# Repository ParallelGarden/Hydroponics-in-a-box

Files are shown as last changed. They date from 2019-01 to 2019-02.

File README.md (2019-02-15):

# Hydroponics-in-a-box

## EXPERIMENTAL DESIGN FEATURE TO GROW PLANTS IN A CAFE

### PURPOSE

This hydroponics box was custom developed to fit under the bar in Bitcoin Coffee at Paralelní Polis in Prague. This hydroponic box uses the drip irrigation principle. It serves as special design feature where vegetables can be grown for the purpose of the cafe, to study production process, to communicate the technology with the public, and to conduct workshops on growing in hydroponics. Thebox was designed in a way to be as compact as possible in order to avoid external solution reservoir, exposed wiring, etc. This project consists of two projects that form a compatible outcome product: hydroponics system itself, and IoT device that is being developed in order to collect data about the growing process, optimize costs, and eventually to take control over the system.

This initiative is a project related to the Enviro Meetup programme we are running in Paralelní Polis in Prague. Our activities are being live streamed through the facebook of Paralelní Polis [https://www.facebook.com/vejdiven/](https://www.facebook.com/vejdiven/) . Then they are being uploaded to youtube under following link: [https://www.youtube.com/watch?v=hhW6fsABNEE&list=PLGJQS0h-wqLQ6r8_6Ans_e26NkKsHYUh-](https://www.youtube.com/watch?v=hhW6fsABNEE&list=PLGJQS0h-wqLQ6r8_6Ans_e26NkKsHYUh-) We would love to enable the content for English speakers as well, and we would appreciate any initiative to help us with translation from Czech to English and subtitles addition into our videos.

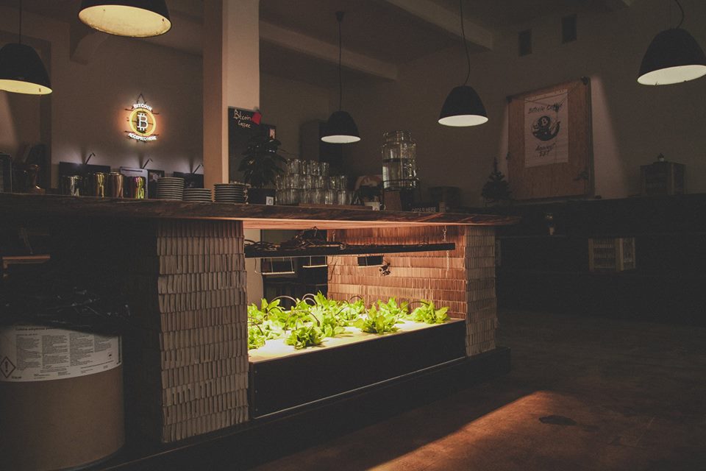
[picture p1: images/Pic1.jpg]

[Photo by: pedro__35mm](https://www.instagram.com/pedro__35mm/)

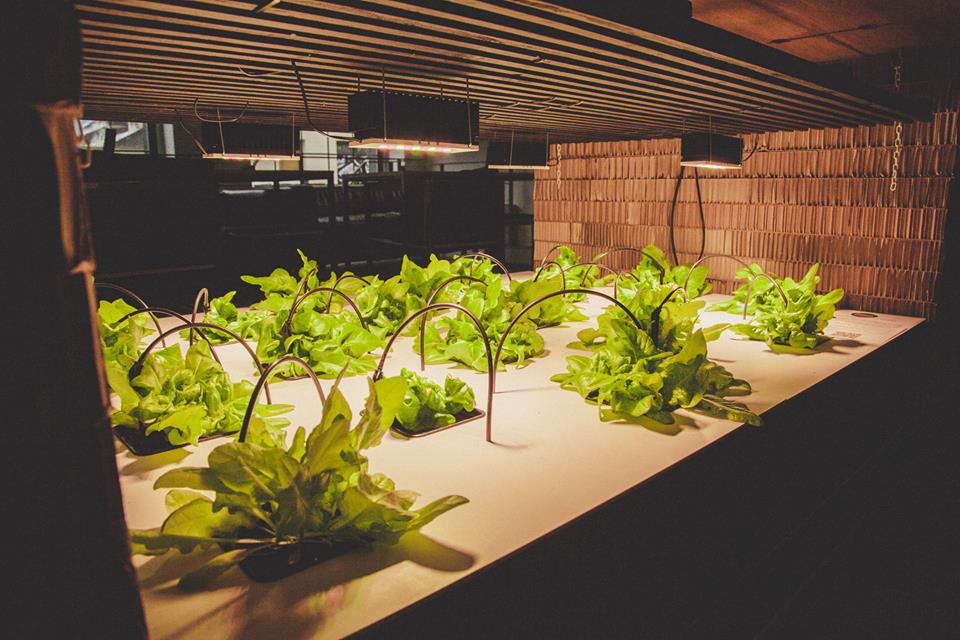
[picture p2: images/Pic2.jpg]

[Photo by: pedro__35mm](https://www.instagram.com/pedro__35mm/)

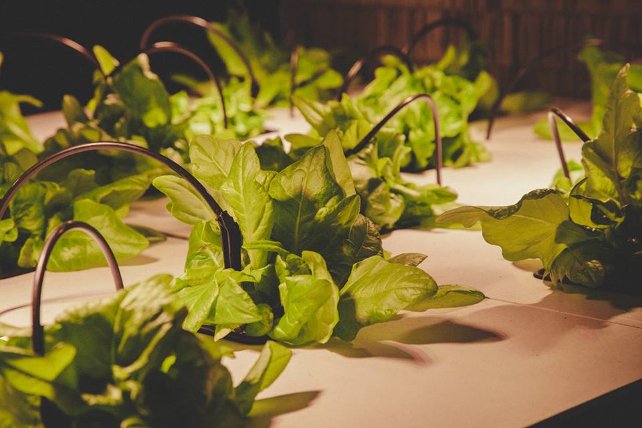
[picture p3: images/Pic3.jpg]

[Photo by: pedro__35mm](https://www.instagram.com/pedro__35mm/)

### OPEN SOURCE REPOSITORIES AND DEVELOPMENT

#### Hydroponics system

Full documentation about this project may be found in the Github repository under following link:  [https://github.com/ParallelGarden/Hydroponics-in-a-box](https://github.com/ParallelGarden/Hydroponics-in-a-box) 

NOTICE! We understand somebody might not be familiar with Github. If you would like to contribute to the development, but don't know how to do so, please feel free to send your suggestions via e-mail: jakub.hamata@gmail.com

##### Development road map:

* Lights - We are overal interested in finding the perfect fit lights for our system to ipmrove the effectivity of the growing system. Crucial deliverables are: cost of the light, electricity consumption, and suitability. Current lights are full spectrum LED which is great for growing both leafy and fruit vegetables. However we need quite many of them due to the space limitation, and they are quite strong (causing little burning of edges of leaves). The angle of the light beam is quite narrow for the space.

* Growing substrates - At the beginning we started with realiable substrates such as coconut fibre substrate, or rockwool cubes. We are interested in finding a substrate that can be produced locally, and is biodegradable. Coconut substrates are the last option as this material has to be imported from other parts of the world.

* Fertilizers - We are looking for an organic fertilizer (or mix of organic fertilizers) to establish the production in bio quality. We are very limited by hygienic standards of the place as it is completely exposed. We must avoid any unpleasand smell or breeding of pests.

* Technologies and processes - Please have a look at our datasheet regarding the cost of the production under following link [https://github.com/ParallelGarden/Hydroponics-in-a-box/blob/master/datasheets/EconomicsOfTheProduction.pdf](https://github.com/ParallelGarden/Hydroponics-in-a-box/blob/master/datasheets/EconomicsOfTheProduction.pdf) We will appreciate any contributions regarding the technology that can reduce production costs or tips to reduce the time consumption of the labour. In case of labour we would like to reduce time consumption on following operations: preparation of seedlings, and regular cleanup of the system.

##### IoT device

Full documentation about this project may be found in the Github repository under following link:[https://github.com/octopusengine/octopusLAB_parallel_garden](https://github.com/octopusengine/octopusLAB_parallel_garden)

Collected database is accessible under following link:

[http://www.octopusengine.org/api/hydrop/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](http://www.octopusengine.org/api/hydrop/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)

Created by Jakub Hamata

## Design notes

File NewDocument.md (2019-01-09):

# New Document

hello world
* gggg
* ggg
* ggg

#
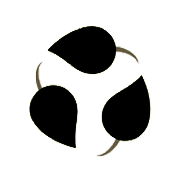
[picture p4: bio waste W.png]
obrazek vole


1. list 1
2. dfdfd
2. fdfdfd
3. gggg
4. gggg

### 444
## ff
###### ssss

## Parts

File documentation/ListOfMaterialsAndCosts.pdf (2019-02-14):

# HYDROPONICS IN THE BOX

## List of materials and costs

Conversion rate: 1USD = 21,5CZK (Jan2019)
Article character: VAR = variable = we encourage to substitute the article by any cheaper, but suitable material

## RESERVOIR

N.O. | Article character | Name | Material specification | Unit | Unit cost (CZK) | Quantity | Total cost (CZK) | Total cost (USD)
1 | FIX | Plywood board | 96x20x2cm (black finish) | each | 173 | 2 | 346 | 16
2 | FIX | Plywood board | 150x20x2cm (black finish) | each | 346 | 2 | 692 | 32
3 | FIX | Screws | 4x40 | each | 2 | 12 | 24 | 1
4 | VAR | Plastic board | 150x100x0,5cm | each | 896 | 1 | 896 | 42
5 | FIX | Screws | 3x40 | each | 2 | 46 | 92 | 4
6 | VAR | Plastic board | 146x96x0,5cm | each | 896 | 1 | 896 | 42
7 | VAR | Plastic board | 146x18x0,5cm | each | 224 | 2 | 448 | 21
8 | VAR | Plastic board | 95x18x0,5cm | each | 224 | 2 | 448 | 21
9 | FIX | Glue for plastics | 0,5l | each | 120 | 1 | 120 | 6
10 | FIX | Plumbers putty | 280ml | each | 144 | 0,4 | 57,6 | 3
4020 187

## MIDDLE FLOOR

N.O. | Article character | Name | Material specification | Unit | Unit cost (CZK) | Quantity | Total cost (CZK) | Total cost (USD)
1 | VAR | Plastic board | 95x72,5x0,5 | each | 448 | 2 | 896 | 42
2 | FIX | Plastic anchors for styrofoam heat insulation | Length 6cm | each | 10 | 21 | 210 | 10
3 | FIX | Plumbers putty | | each | 144 | 0,3 | 43,2 | 2
Total | | | | | | | 1149 53

## TOP BOARD

N.O. | Article character | Name | Material specification | Unit | Unit cost (CZK) | Quantity | Total cost (CZK) | Total cost (USD)
1 | FIX | Plastic board | 75x100x0,5 | each | 448 | 2 | 896 | 42
2 | FIX | Plastic board | 72,5x95x0,5 | each | 448 | 2 | 896 | 42
3 | FIX | Plastic anchors for styrofoam heat insulation | Length 12,5cm | each | 10 | 10 | 100 | 5
4 | FIX | Plumbers putty | | each | 144 | 0,15 | 22 | 1
Total | | | | | | | 1914 89

Total

## IRRRIGATION

N.O. | Article character | Name | Material specification | Unit | Unit cost (CZK) | Quantity | Total cost (CZK) | Total cost (USD)
1 | FIX | Plastic pipe holder | Diameter 1,5cm | each | 5,5 | 14 | 77 | 4
2 | FIX | Plastic pipe | Diameter 1,5cm | m | 8,5 | 6 | 51 | 2
3 | FIX | Plastic pipe L connection | Diameter 1,5cm | each | 15 | 8 | 120 | 6
4 | FIX | Plastic pipe T connection | Diameter 1,5cm | each | 39 | 2 | 78 | 4
5 | FIX | Plastic hose | Diameter 1,5cm | m | 35 | 1 | 35 | 2
6 | FIX | Plastic hose L connections | Diameter 1,5cm | each | 39 | 2 | 78 | 4
7 | FIX | Plastic flow regulator | 4L/h | each | 12 | 22 | 264 | 12
8 | FIX | Plastic capillary pipes | | m | 10 | 6,3 | 63 | 3
9 | FIX | Plastic dripping needle | | each | 5 | 21 | 105 | 5
10 | FIX | Super glue | | each | 90 | 1 | 90 | 4
11 | FIX | Submersible water pump | 750l/h | each | 399 | 1 | 399 | 19
12 | FIX | Lever cable connecter | | each | 20 | 2 | 40 | 2
13 | FIX | Analog timer | | each | 100 | 1 | 100 | 5
Total | | | | | | | 1500 70

## LIGHTING SYSTEM

N.O. | Article character | Name | Material specification | Unit | Unit cost (CZK) | Quantity | Total cost (CZK) | Total cost (USD)
1 | FIX | Wooden prism | 150x2x2cm | each | 48 | 17 | 816 | 38
2 | FIX | Wooden prism | 99x5x2cm | each | 62 | 3 | 186 | 9
3 | FIX | Nails | 3cm | each | 1 | 51 | 51 | 2
4 | FIX | Steel hooks with screw | | each | 2 | 4 | 8 | 1
5 | VAR | Full spectrum LED lights | SANlight M30 30W | each | 3599 | 4 | 14396 | 670
6 | FIX | Analog timer | | each | 100 | 1 | 100 | 5
Total | | | | | | | 15557 724
| CZK | USD
TOTAL | 24139 | 1123

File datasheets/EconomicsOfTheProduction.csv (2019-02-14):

ECONOMICS OF THE PRODUCTION
Leaf lettuce result per harvest
Growing period: 10 days seedlings preparation + 21 days growing in the hydroponics system
Conversion rate: 1USD = 21,5CZK (Jan2019)
COSTS
N.O. | Material | Work | Specification | Unit | Unit cost CZK | Quantity | Cost CZK | Cost USD
1 | Electricity |  |  | 1 kWh | 5 | 30,24 | 151 | 7
2 | Water |  |  | 1 m3 | 89,66 | 0,07 | 6 | 0
3 | Fertilizer |  | General Hydroponics FloraNova Grow 473ml /16 OZ | each | 529 | 0,14 | 74 | 3
4 | Substrate |  | Rockwool cube 3,6 x 3,6cm | each | 4 | 21 | 84 | 4
5 | Seeds |  |  | package | 15 | 0,1 | 2 | 0
6 |  | Sowing | NET income 20.000CZK/month | h | 230 | 0,25 | 58 | 3
7 |  | Planting | NET income 20.000CZK/month | h | 230 | 0,75 | 173 | 8
8 |  | System checking | NET income 20.000CZK/month | h | 230 | 1 | 230 | 11
9 |  | System maintenance | NET income 20.000CZK/month | h | 230 | 1 | 230 | 11
TOTAL COST: |  |  |  |  |  |  | 1007CZK | 47USD
WORK: |  |  |  |  |  |  | 690CZK | 32USD
ENERGIES AND MATERIALS: |  |  |  |  |  |  | 317CZK | 15USD
REVENUE
N.O. | Product | Unit | Quantity | Usual retail price CZK | Revenue CZK | Revenue in USD
1 | Lettuce | each | 21 | 30 | 630 | 29
RESULT
1) | In current setup it is not possible to become profitable with usual retail price of lettuce. One lettuce has to be sold for at least 48CZK / 2,23USD.
2) | Main articles are: electricity consumption, and labour. Reduction in these articles could bring positive result.
COMMENTS
1) | It was not inteded to create positive economical outcome with the first hydroponic system.
2) | Hydroponic system brings also other values than just money.
3) | Very likely it is possible to sell the product for higher price than usual retail price of conventional agriculture product.
4) | It would be a great success to manage to reduce production costs to end up on even result (no profit, and no loss).
POTENTIAL OF CURRENT TECHNOLOGY
If we had more space available we could grow twice as many lettuces with only slight increment of the investment cost (larger box), same amount of lights, etc.
Find below a study for double sized box:
COSTS
N.O. | Material | Work | Specification | Unit | Unit cost CZK | Quantity | Cost CZK | Cost USD
1 | Electricity |  |  | 1 kWh | 5 | 30,24 | 151 | 7
2 | Water |  |  | 1 m3 | 89,66 | 0,07 | 6 | 0
3 | Fertilizer |  | General Hydroponics FloraNova Grow 473ml /16 OZ | each | 529 | 0,14 | 74 | 3
4 | Substrate |  | Rockwool cube 3,6 x 3,6cm | each | 4 | 42 | 168 | 8
5 | Seeds |  |  | package | 15 | 0,2 | 3 | 0
6 |  | Sowing | NET income 20.000CZK/month | h | 230 | 0,5 | 115 | 5
7 |  | Planting | NET income 20.000CZK/month | h | 230 | 1,5 | 345 | 16
8 |  | System checking | NET income 20.000CZK/month | h | 230 | 1 | 230 | 11
9 |  | System maintenance | NET income 20.000CZK/month | h | 230 | 1,5 | 345 | 16
TOTAL COST: |  |  |  |  |  |  | 1438CZK | 67USD
WORK: |  |  |  |  |  |  | 1035CZK | 48USD
ENERGIES AND MATERIALS: |  |  |  |  |  |  | 403CZK | 19USD
REVENUE
N.O. | Product | Unit | Quantity | Usual retail price CZK | Revenue CZK | Revenue in USD
1 | Lettuce | each | 42 | 30 | 1260 | 59
RESULT
1) | In current setup it is not possible to become profitable with usual retail price of lettuce. One lettuce has to be sold for at least 35CZK / 1,63USD.
2) | Optimization of cost of labour, substrate, fertilizer, and utilization of daylight appear to be a way to find a profitable model.
3) | Shortening the period of having lettuce in the system also appears to be a way to rech even or positive result.
4) | Another way to go might be to chose a different crop to grow.

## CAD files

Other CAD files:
documentation/dwg drawing/HydroponicsInTheBox1.0.dwg

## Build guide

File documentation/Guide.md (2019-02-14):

# STEP BY STEP GUIDE

## INTRODUCTION

This hydroponic system was developed as a custom design feature for Bitcoin Coffee in Parallel Polis. It is meant to supply the Cafe with specific vegetables that are being used there (mostly leaf vegetables). It also serves for experiments that are combining growing in hydroponic system, IoT technologies, and open source in order to reach as much autonomity of the system as possible that is able to optimize growing process, and energy consumption to the most reasonable effectivity.







## TOOLS

* Drilling machine
* Screw driver
* Glue gun (depending of the type of the glue)
* Paint brush (10cm or wider)
* NT cutter
* Personal protection equipment

## RESERVOIR CONSTRUCTION

### LIST OF MATERIALS:

* Plywood board 96x20x2cm 2PCS
* Plywood board 150x20x2cm 	2PCS
* Screws for wood 4x40 		12PCS
* Plastic board (used plastic banner) 150x100x0,5cm	1PC
* Screws for the wood 3x40	46PCS
* Plastic board (used plastic banner) 146x96x0,5cm 	1PC
* Plastic board (used plastic banner) 146x18x0,5cm 	2PCS
* Plastic board (used plastic banner) 95x18x0,5cm 	2PCS
* Glue for plastics		0,5L
* Plumbers putty			280ml

### PROCEDURE:

#### Step 1	
Construct the basic frame of the box out of the plywood. Fix each side evenly with 3 screws 4x40. To avoid rupture of the plywood it is recommended to drill a hole of slightly smaller diameter than the diameter of the screw. When completed, dril a hole for pump cable in the upper half of the box height (as per drawing).

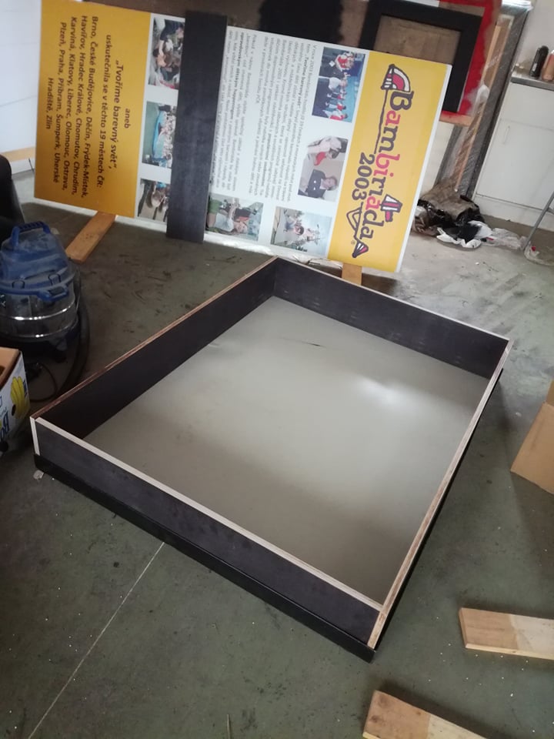
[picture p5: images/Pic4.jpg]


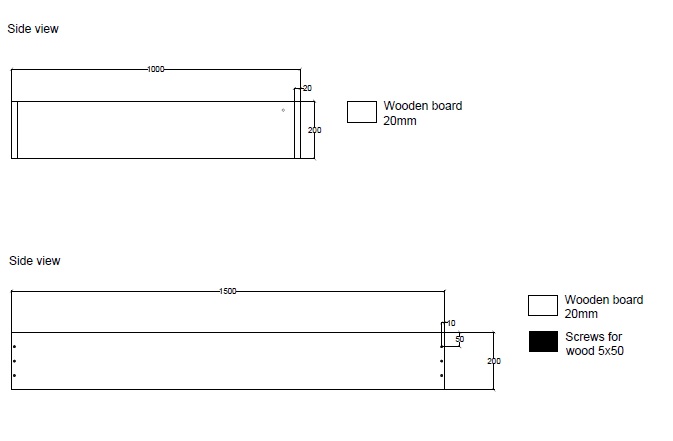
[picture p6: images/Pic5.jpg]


#### Step 2	
Attach the plastic board  (150x100cm) to the wooden frame to create first layer of the bottom. Use glue and screws 3x40. Screws shall be placed in 10cm distance from each other.

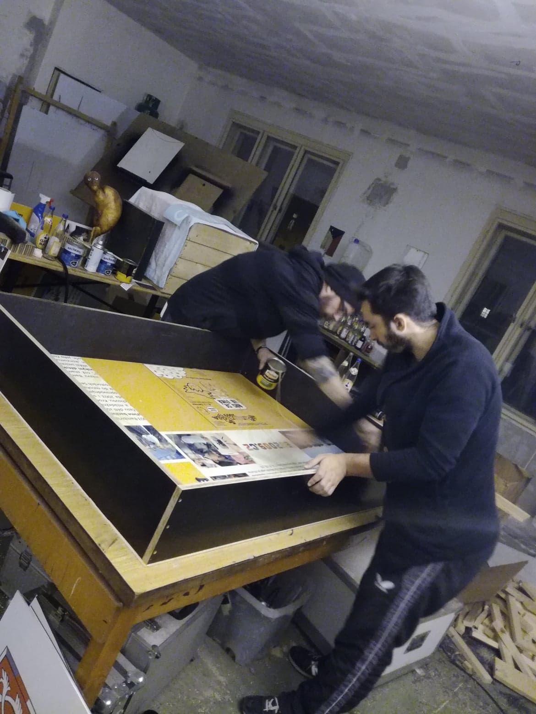
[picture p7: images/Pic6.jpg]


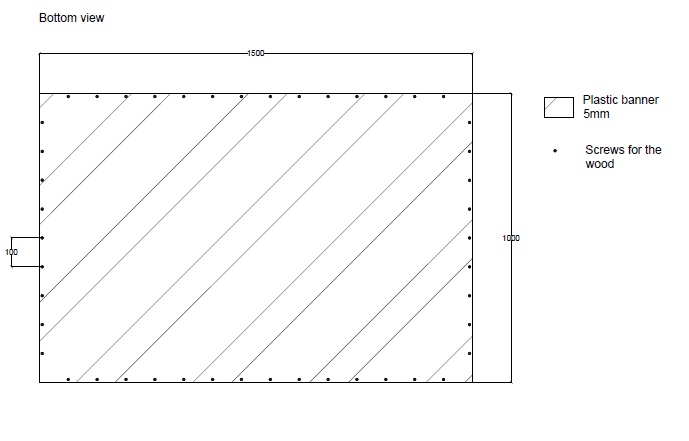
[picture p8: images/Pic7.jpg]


#### Step 3	
Glue another plastic board (146x96cm) on the top of the bottom plastic board to create second layer of the bottom. Blank side should face up.

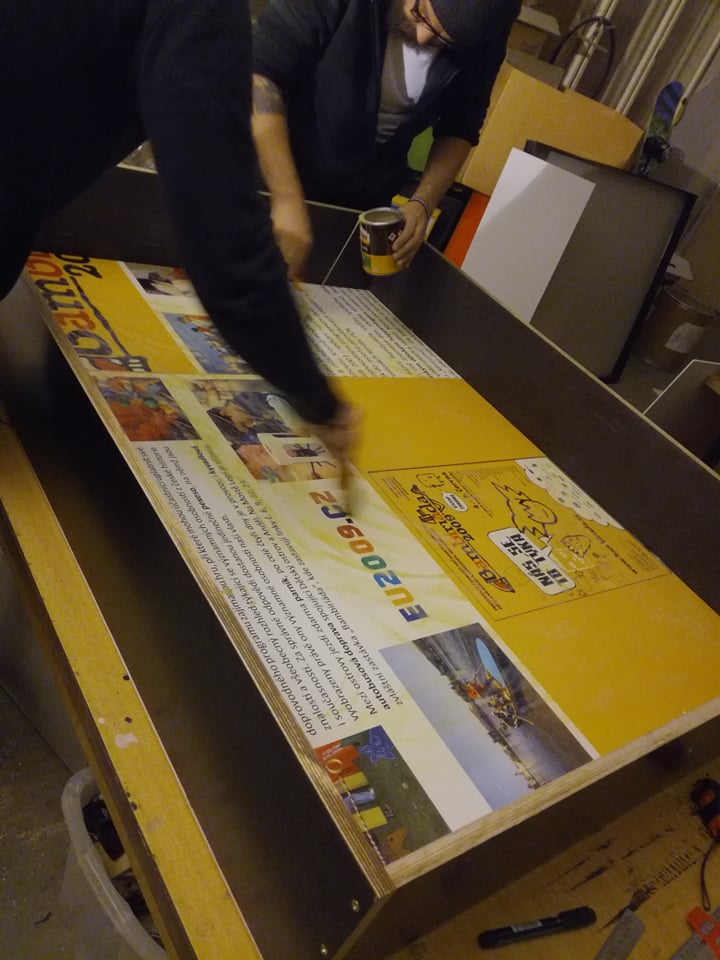
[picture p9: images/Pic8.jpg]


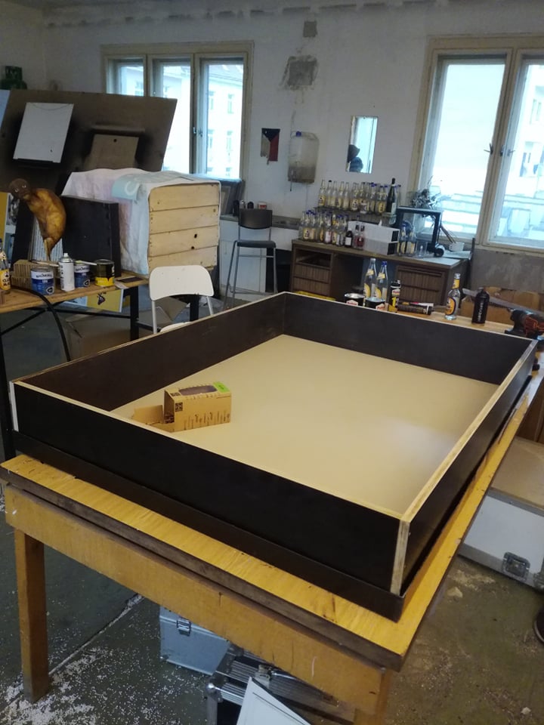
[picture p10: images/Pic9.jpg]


#### Step 4	
Glue plastic boards (146x18x0,5cm and 95x18x0,5cm) on sides of the box from the inside.

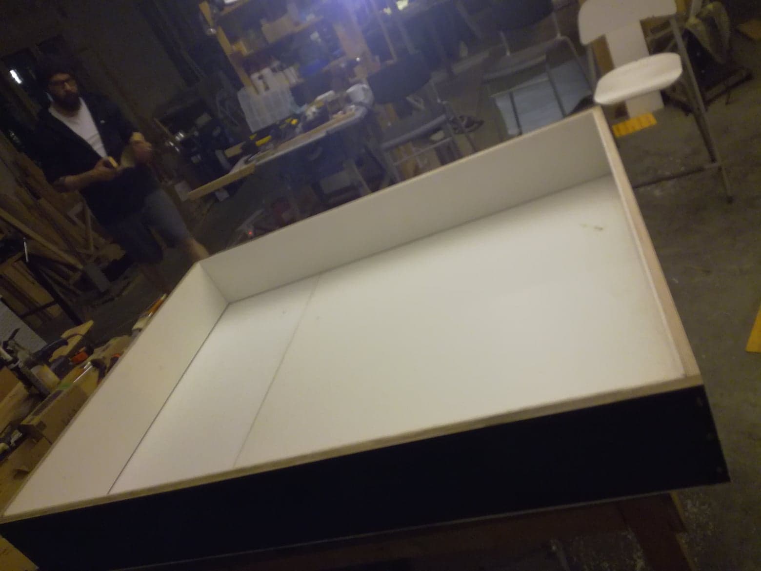
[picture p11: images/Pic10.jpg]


#### Step 5	
Seal all gaps with plumbers putty to seal the reservoir. Repeat this operation couple of times to make sure the reservoir will be waterproof. TIP: Once this step is done conduct a leakage test by filling the reservoir with water to the level of 11cm of depth and look for any leakage.

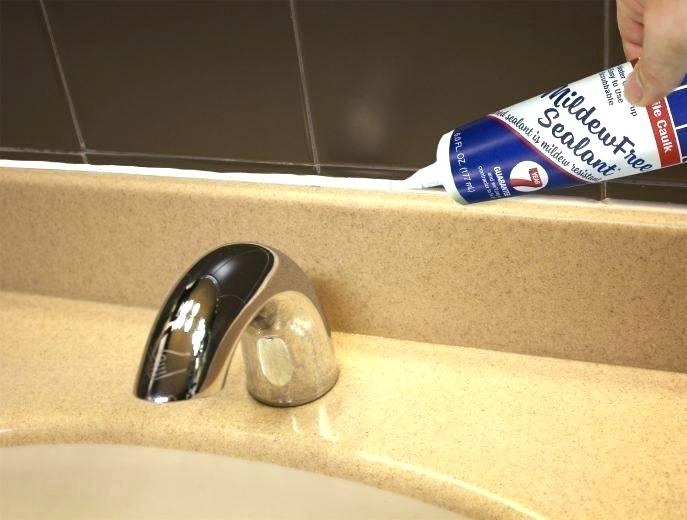
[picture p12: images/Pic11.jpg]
Illustrative_photo


#### REFERENCE	 
Refer to the drawing Reservoir for more information.

## MIDDLE FLOOR

### LIST OF MATERIALS:

* Plastic board (used plastic banner) 95x72,5x0,5cm		 2PCS
* Plastic anchors for styrofoam heat insulation Length 6cm 	21PCS
* Plumbers putty		280ml

### PROCEDURE:

#### Step 1	
Take one plastic board and cut away two corners. Corners are being cut away to create passage for the irrigation pipeline, and to create access to the growing solution for monitoring.

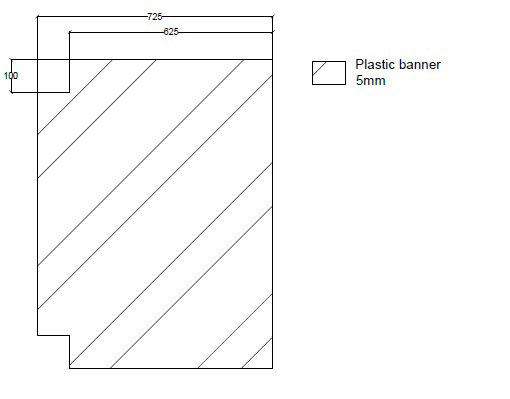
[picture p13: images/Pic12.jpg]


#### Step 2	
Cut plastic anchors to the length of 6cm and glue them to both boards with plumbers putty.

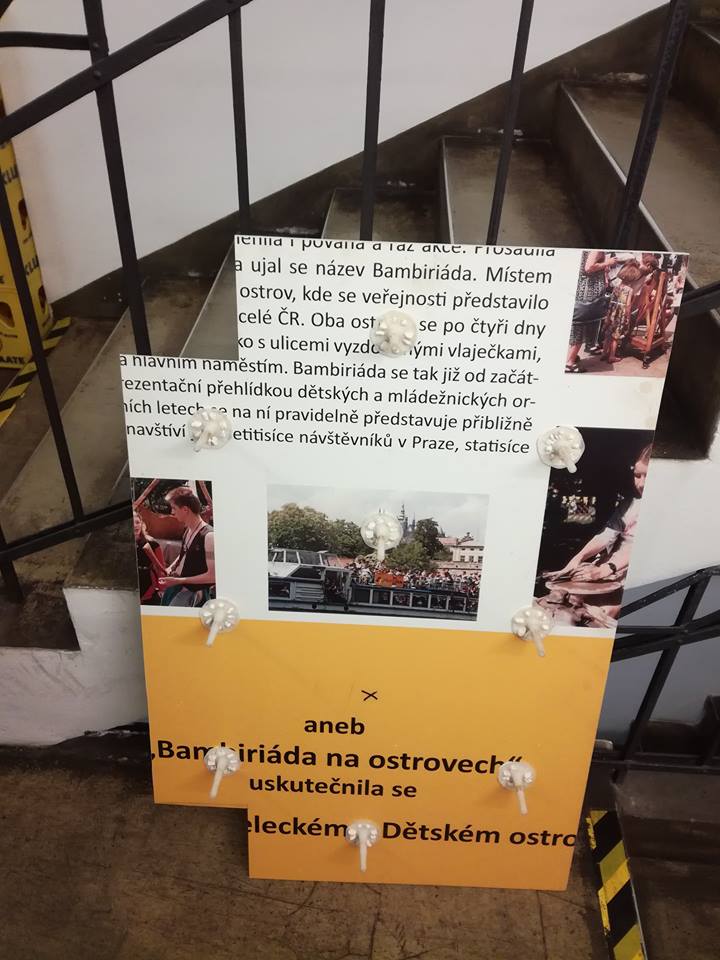
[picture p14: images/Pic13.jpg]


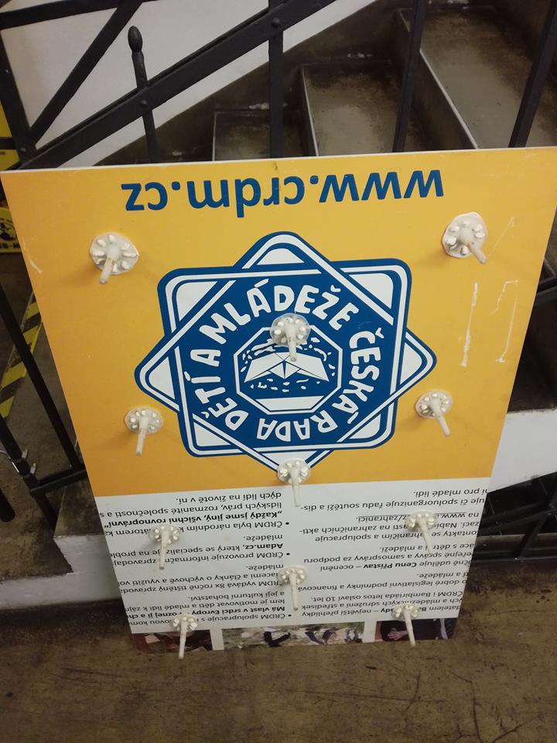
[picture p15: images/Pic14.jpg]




#### REFERENCE	
Refer to the drawing Middle Floor Construction for more information.

## TOP BOARD

### LIST OF MATERIALS:

* Plastic board (used plastic banner) 75x100x0,5cm 		2PCS
* Plastic board (used plastic banner) 72,5x95x0,5cm 		2PCS
* Glue for plastics
* Plastic anchors for styrofoam heat insulation Length 12,5cm 	10PCS
* Plumbers putty

### PROCEDURE:

#### Step 1	
Glue smaller plastic boards to the bottom of larger ones. One edge should be aligned with the larger board while leaving even 2,5cm gap on other three sides.

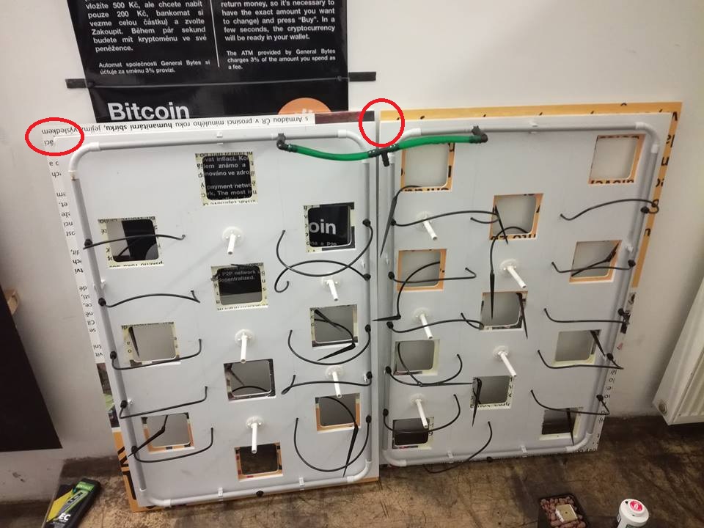
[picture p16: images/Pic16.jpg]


#### Step 2	
Cut away holes for pots and irrigation capillary pipes. 

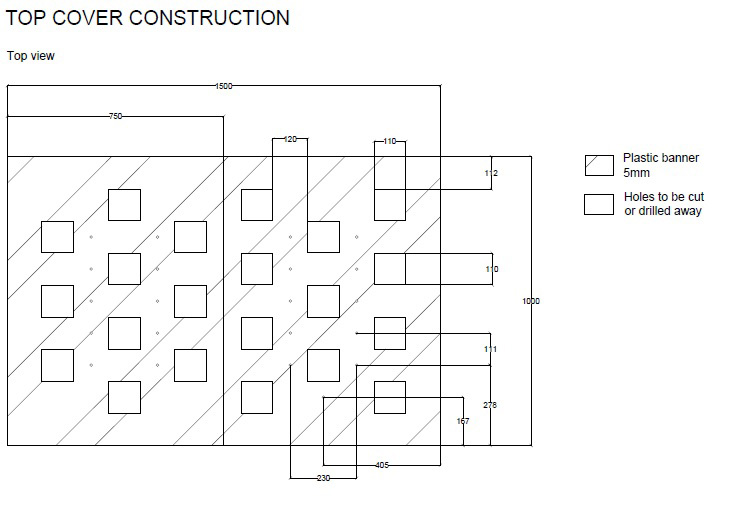
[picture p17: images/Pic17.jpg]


#### Step 3	
Cut plastic anchors to the length of 12,5cm and glue them with plumbers putty or super glue to the bottom of both plastic boards.

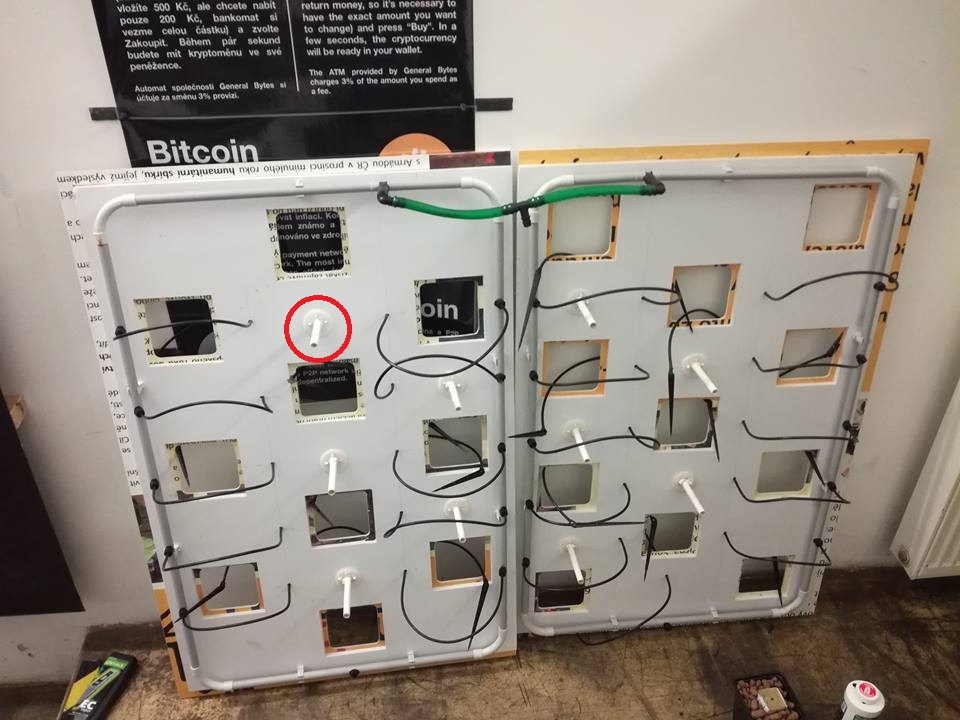
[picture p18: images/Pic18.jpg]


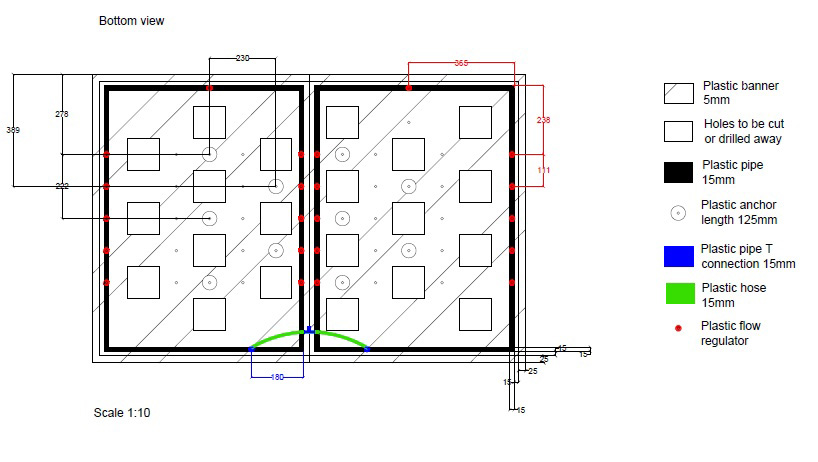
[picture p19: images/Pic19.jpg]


#### REFERENCE	
Refer to the drawing Top Board Construction for more information.

## IRRIGATION

### LIST OF MATERIALS:

* Plastic pipe diameter 1,5cm holder 		14PCS
* Plastic pipe diameter 1,5cm			6m
* Plastic pipe L connection diameter 1,5cm 	8PCS
* Plastic pipe T connections diameter 1,5cm 	3PCS
* Plastic hose diameter 1,5cm 			1m
* Plastic hose L connections 			2PCS
* Plastic flow regulator				22PCS
* Plastic capillary pipes 30cm 			21PCS
* Dripping needles 				21PCS
* Super glue 					1PC
* Submersible water pump 750l/h		1PC
* Lever cable connectors 				2PCS

### PROCEDURE:

#### Step 1	
Glue plastic pipe holders to the bottom of the board (7pcs per board) with super glue.

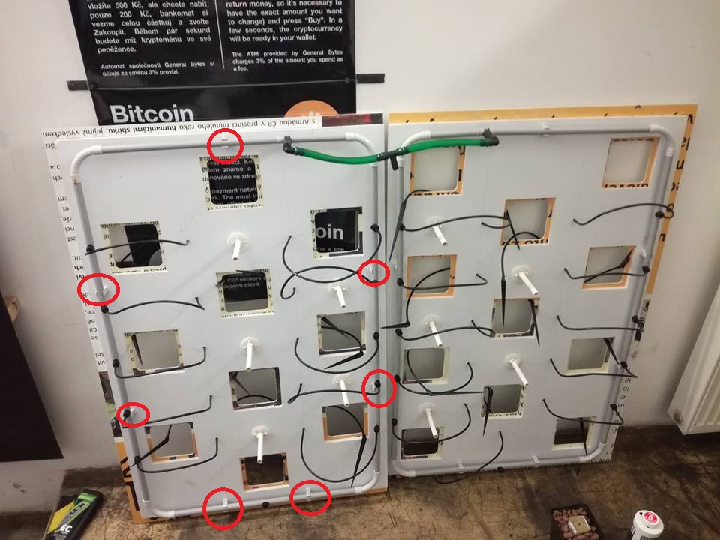
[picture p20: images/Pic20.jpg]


#### Step 2	
Cut plastic pipe in 4 pieces of 89cm and 4 pices of 66cm and connect them with L connections. Create two rectangular pipeline circuits.

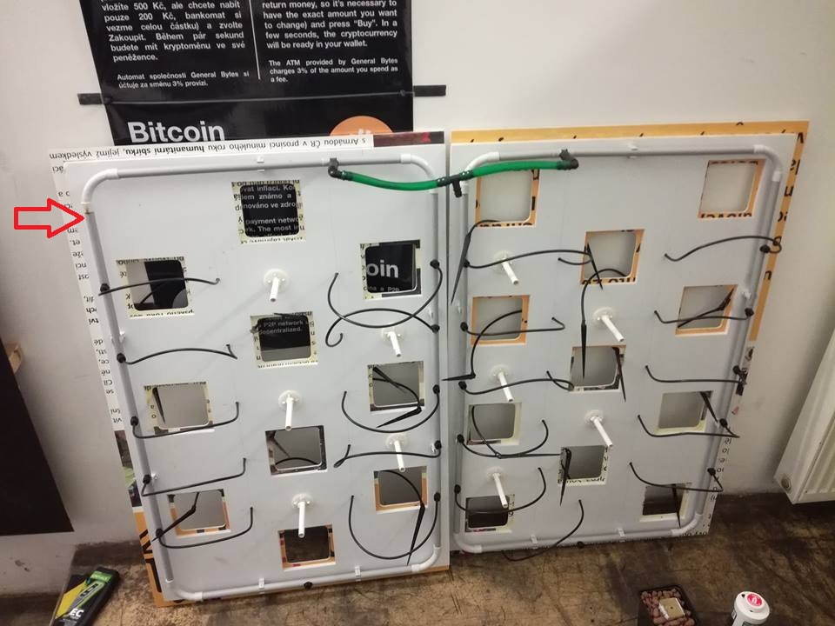
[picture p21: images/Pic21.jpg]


#### Step 3	
Cut two shorter plastic pipes and insert T connection.

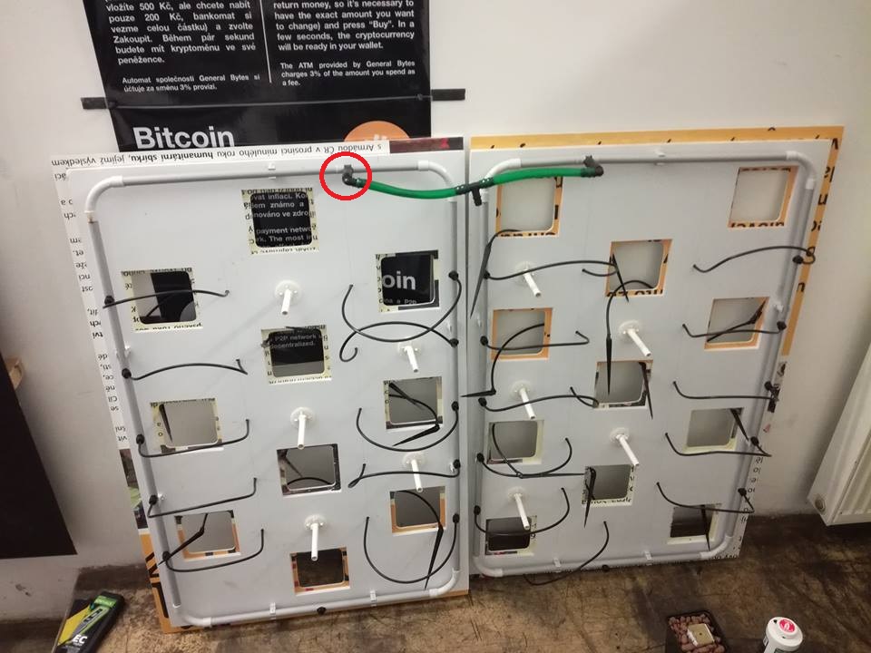
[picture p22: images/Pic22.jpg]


#### Step 4	
Drill small holes into the pipeline and insert flow regulators. Holes should be placed with similar distance to ensure even solution delivery. Note: One module should feed 11 plants, and the other one only 10. To distribute the solution evenly, install 11 flow regulators on both pipeline modules. The extra flow regulator installed in the growing board that feeds only 10 plants will be kept unused.

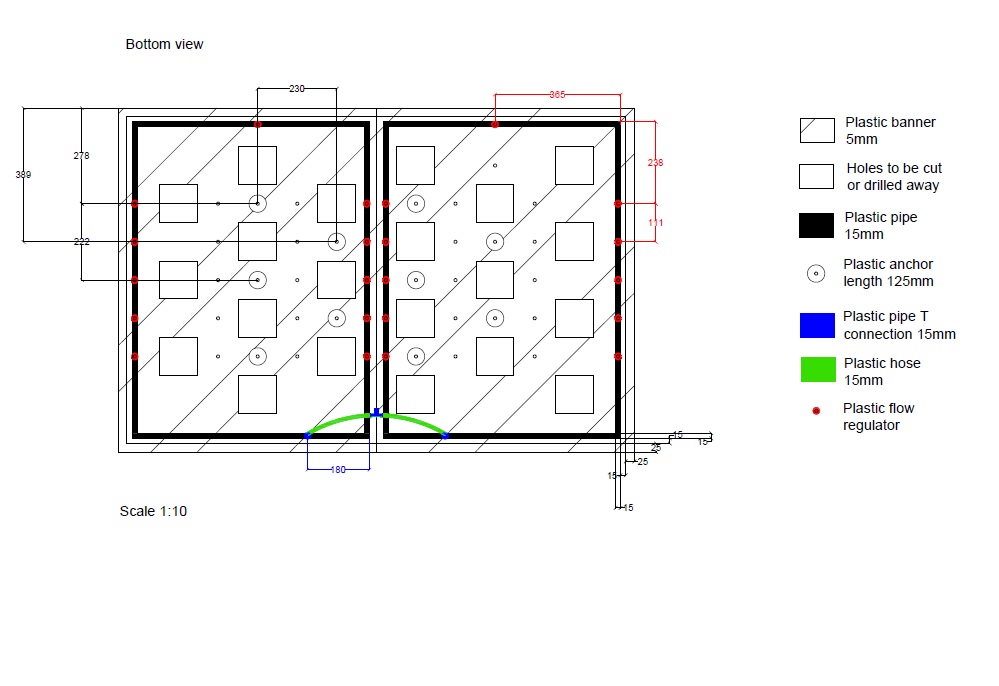
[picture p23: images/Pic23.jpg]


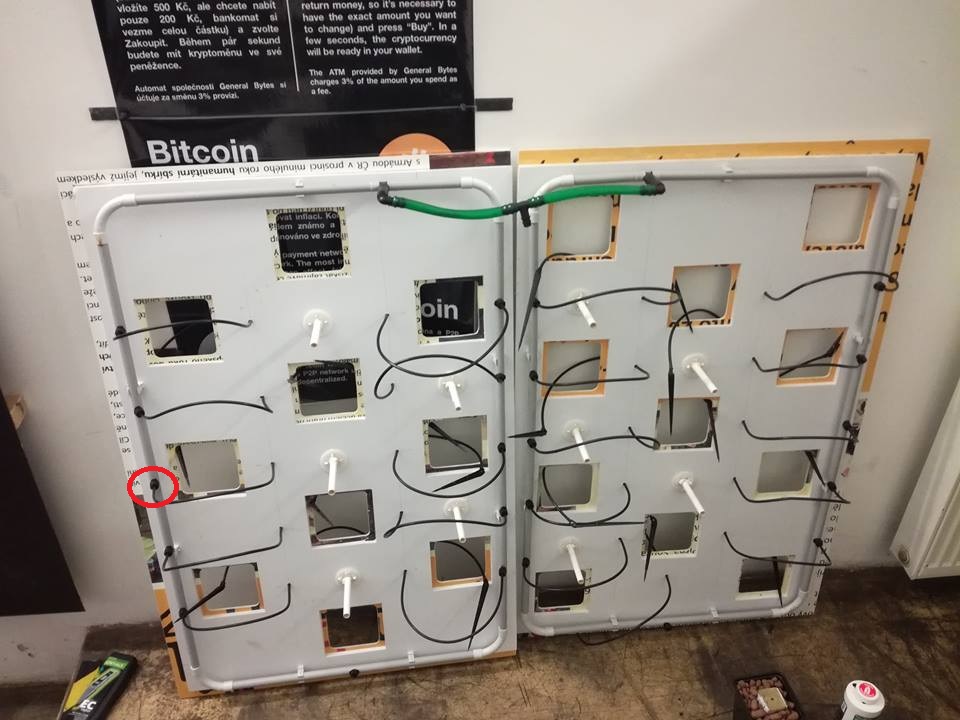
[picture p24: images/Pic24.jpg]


#### Step 5	
Attach capillary pipes to flow regulators and put them through holes in the board. Then you may attach dripping needles to blank ends of capillary pipes. Note: One flow regulator on the board with 10 pot holes will remain blank.

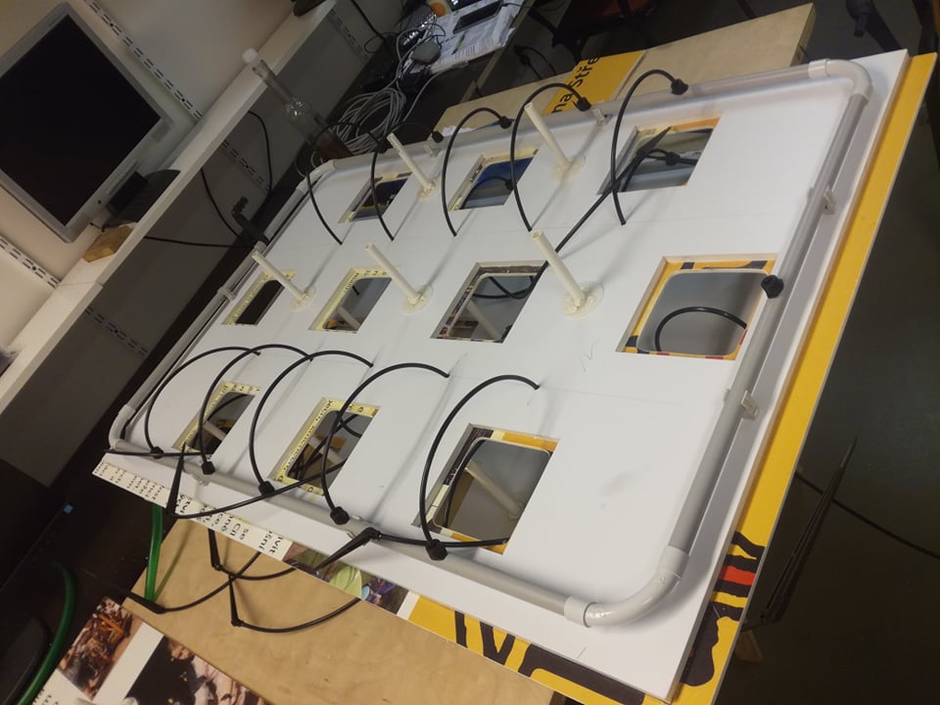
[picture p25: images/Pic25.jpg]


#### Step 6	
Finalize the construction with attaching the hose to inlets of pipeline modules. At the end use one T connection to join pipeline modules to one inlet. Hose should not be folded over to avoid water to move through the system easily.

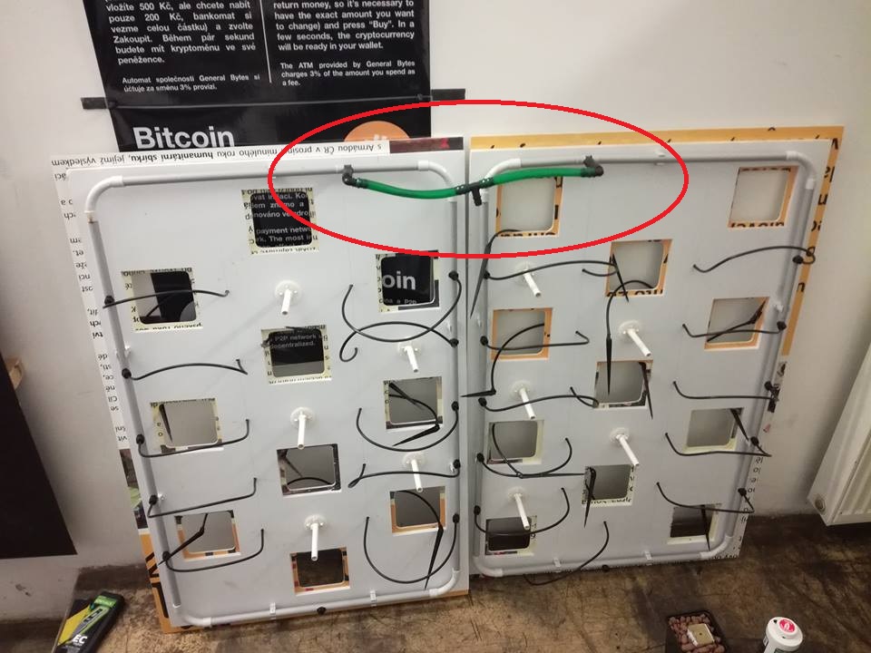
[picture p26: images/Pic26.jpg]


#### Step 7	
Cut the power cable of the pump near the socket plug, put the pump into the box and push the cable through the cable hole in the box. Join the cable again with cable connections.

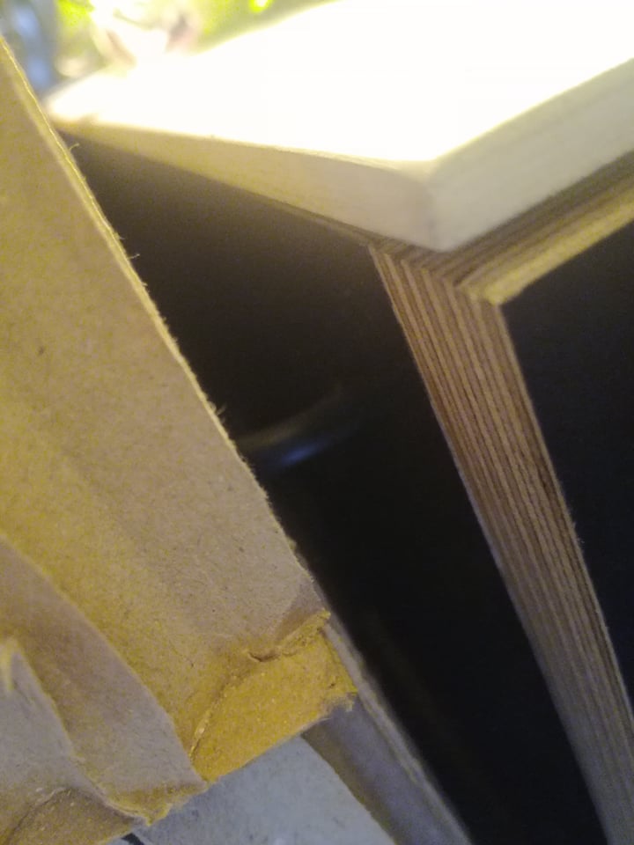
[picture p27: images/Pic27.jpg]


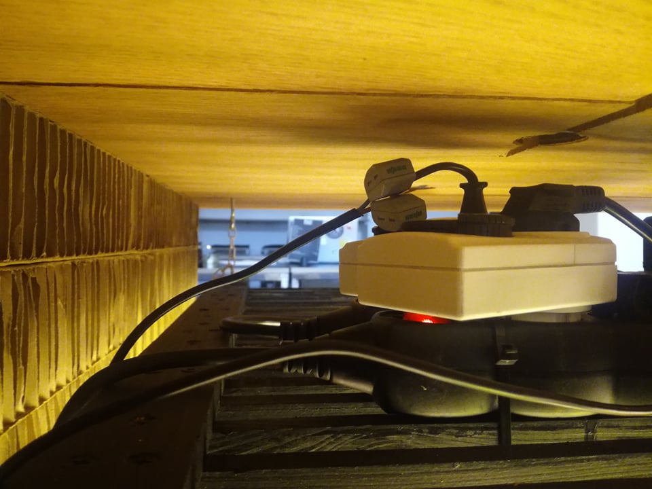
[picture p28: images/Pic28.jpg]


#### Step 8	
Assemble the system. Put the middle floor inside the box and then install the top board.

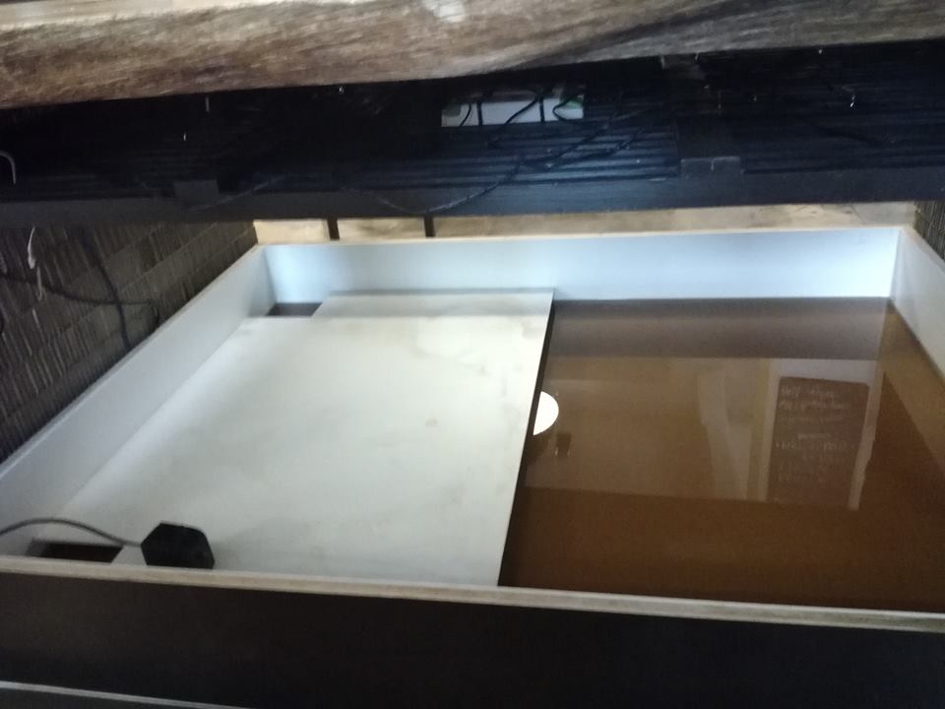
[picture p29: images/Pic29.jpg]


#### Step 9	
Connect the hose to the pump outlet.

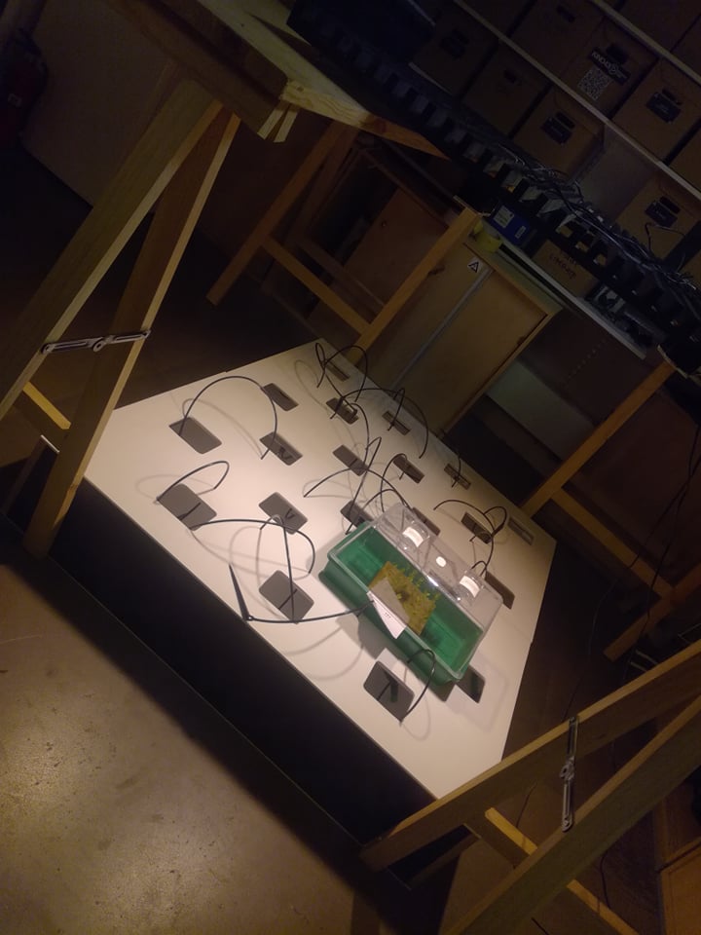
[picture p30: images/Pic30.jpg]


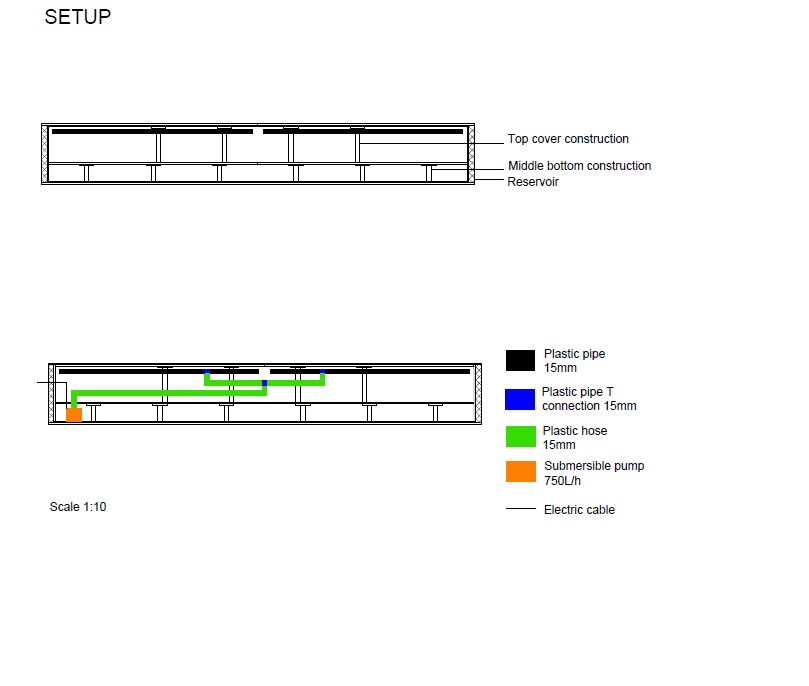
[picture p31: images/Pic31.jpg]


#### REFERENCE:	
Refer to drawings Top Board Construction and Setup for more information.

# LIGHTING SYSTEM

## LIST OF MATERIALS:

* Wooden prism 150x3x2cm 			17PCS
* Wooden prism 99x5x2cm 			3PCS
* Nails length 3cm 				51PCS
* Steel hooks with screws 			4PCS
* Full spectrum LED lights SANlight M30 30W	4PCS

### PROCEDURE:

#### Step 1	
Construct a grid  out ouf wooden prisms with nails, and attach steel hooks to the top of the grid as per drawings.

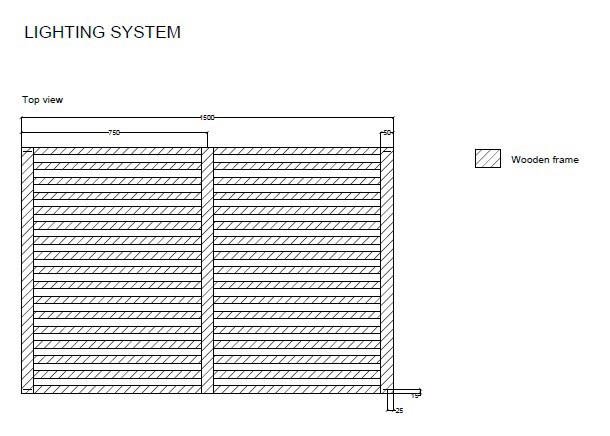
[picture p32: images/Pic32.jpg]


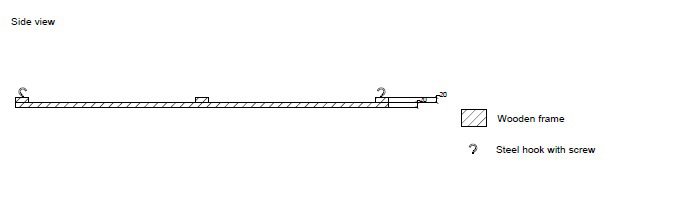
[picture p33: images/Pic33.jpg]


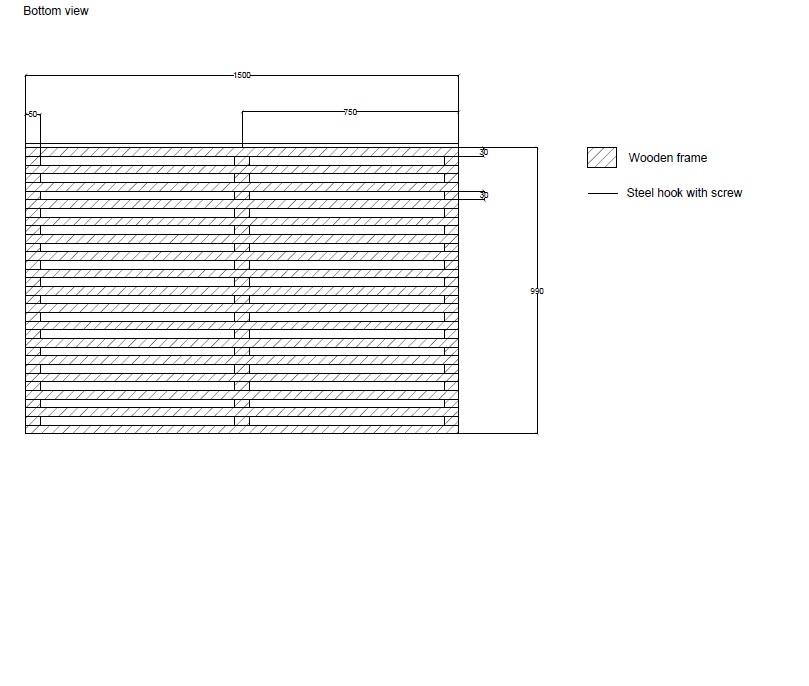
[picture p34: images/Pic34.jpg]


#### Step 2	
Hang wooden contruction to the ceiling.

#### Step 3	
Attach lights to the construction and lead cables as needed.

#### REFERENCE	
Refer to the drawing Lighting System for more information.

### HAVE FUN ;)

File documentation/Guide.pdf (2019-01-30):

# STEP BY STEP GUIDE

## INTRODUCTION

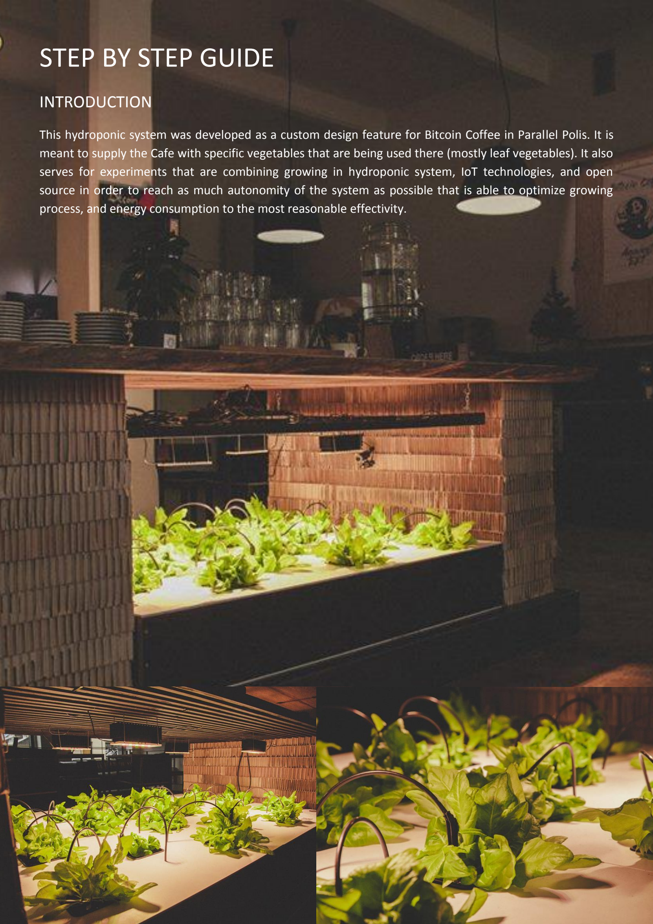
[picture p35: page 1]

This hydroponic system was developed as a custom design feature for Bitcoin Coffee in Parallel Polis. It is meant to supply the Cafe with specific vegetables that are being used there (mostly leaf vegetables). It also serves for experiments that are combining growing in hydroponic system, IoT technologies, and open source in order to reach as much autonomity of the system as possible that is able to optimize growing process, and energy consumption to the most reasonable effectivity.

## TOOLS

- Drilling machine
- Screw driver
- Glue gun (depending of the type of the glue)
- Paint brush (10cm or wider)
- NT cutter
- Personal protection equipment

## RESERVOIR CONSTRUCTION

LIST OF MATERIALS:

- | Plywood board 96x20x2cm | 2PCS
- | Plywood board 150x20x2cm | 2PCS
- | Screws for wood 4x40 | 12PCS
- | Plastic board (used plastic banner) 150x100x0,5cm | 1PC
- | Screws for the wood 3x40 | 46PCS
- | Plastic board (used plastic banner) 146x96x0,5cm | 1PC
- | Plastic board (used plastic banner) 146x18x0,5cm | 2PCS
- | Plastic board (used plastic banner) 95x18x0,5cm | 2PCS
- | Glue for plastics | 0,5L
- | Plumbers putty | 280ml

PROCEDURE:

Step 1 Construct the basic frame of the box out of the plywood. Fix each side evenly with 3 screws 4x40. To avoid rupture of the plywood it is recommended to drill a hole of slightly smaller diameter than the diameter of the screw. When completed, dril a hole for pump cable in the upper half of the box height (as per drawing).

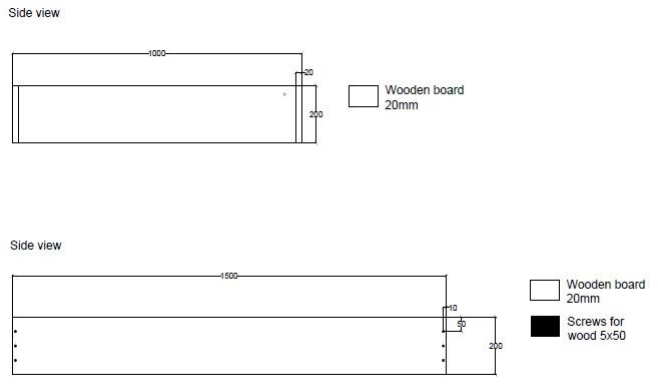
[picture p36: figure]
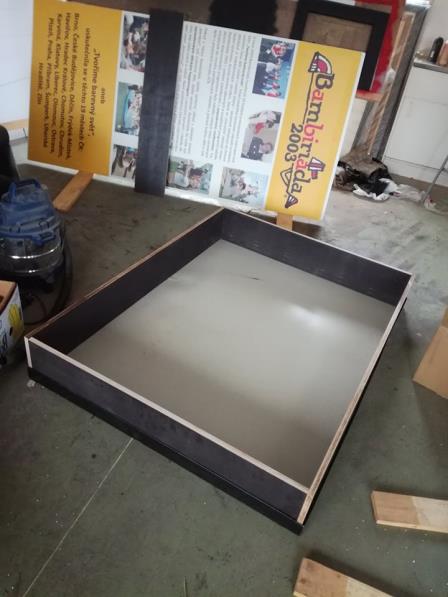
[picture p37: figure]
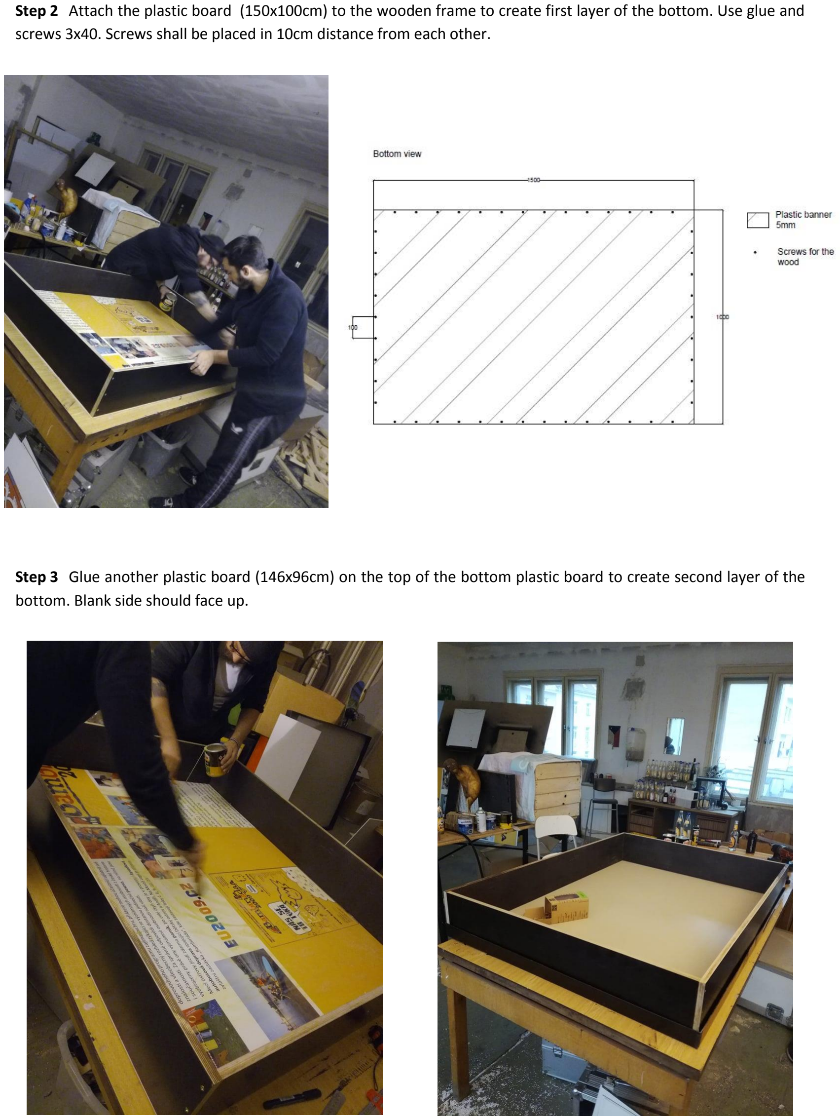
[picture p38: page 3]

Step 2 Attach the plastic board (150x100cm) to the wooden frame to create first layer of the bottom. Use glue and screws 3x40. Screws shall be placed in 10cm distance from each other.
Step 3 Glue another plastic board (146x96cm) on the top of the bottom plastic board to create second layer of the bottom. Blank side should face up.

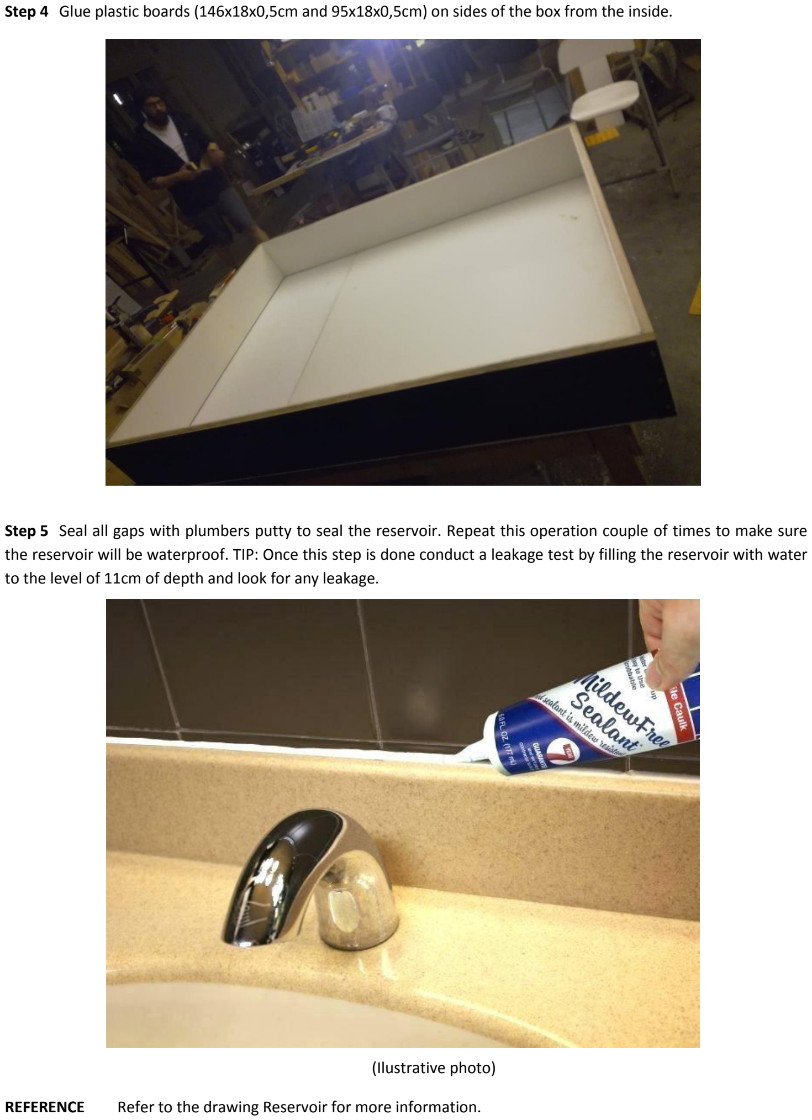
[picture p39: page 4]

Step 4 Glue plastic boards (146x18x0,5cm and 95x18x0,5cm) on sides of the box from the inside.
Step 5 Seal all gaps with plumbers putty to seal the reservoir. Repeat this operation couple of times to make sure the reservoir will be waterproof. TIP: Once this step is done conduct a leakage test by filling the reservoir with water to the level of 11cm of depth and look for any leakage.

(Ilustrative photo)

REFERENCE Refer to the drawing Reservoir for more information.

## MIDDLE FLOOR

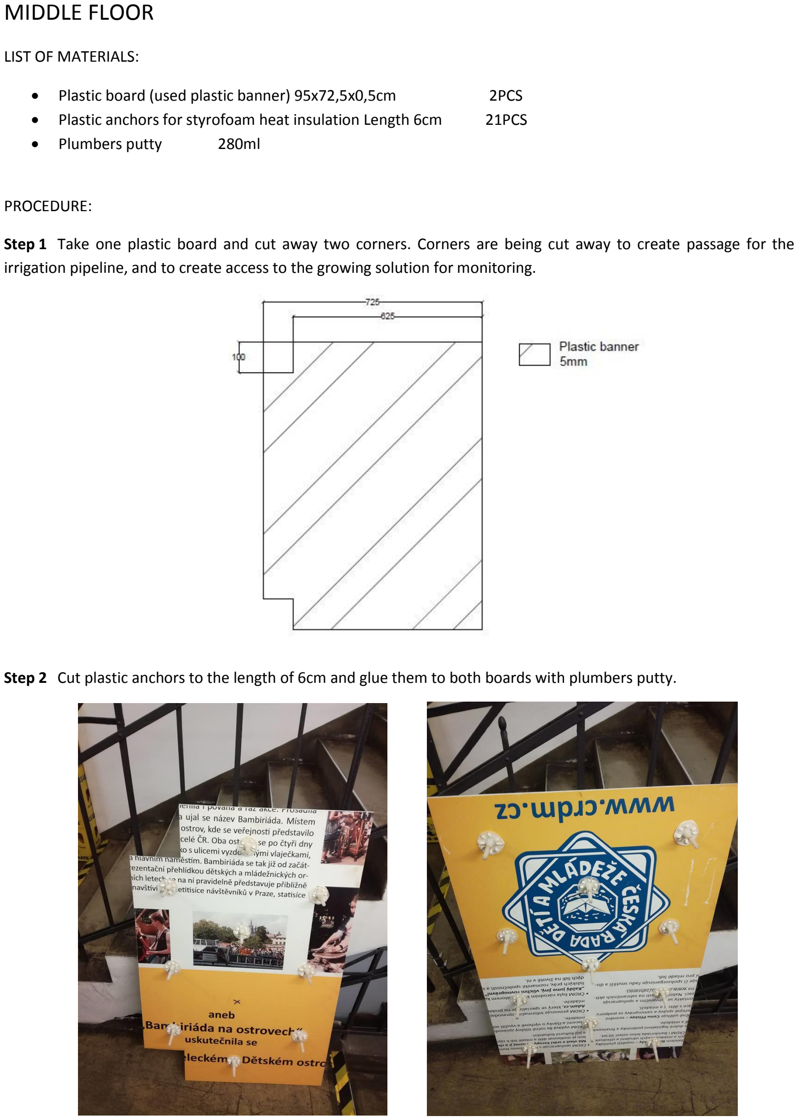
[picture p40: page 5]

LIST OF MATERIALS:

- | Plastic board (used plastic banner) 95x72,5x0,5cm | 2PCS
- | Plastic anchors for styrofoam heat insulation Length 6cm | 21PCS
- | Plumbers putty | 280ml

PROCEDURE:

Step 1 Take one plastic board and cut away two corners. Corners are being cut away to create passage for the irrigation pipeline, and to create access to the growing solution for monitoring.
Step 2 Cut plastic anchors to the length of 6cm and glue them to both boards with plumbers putty.

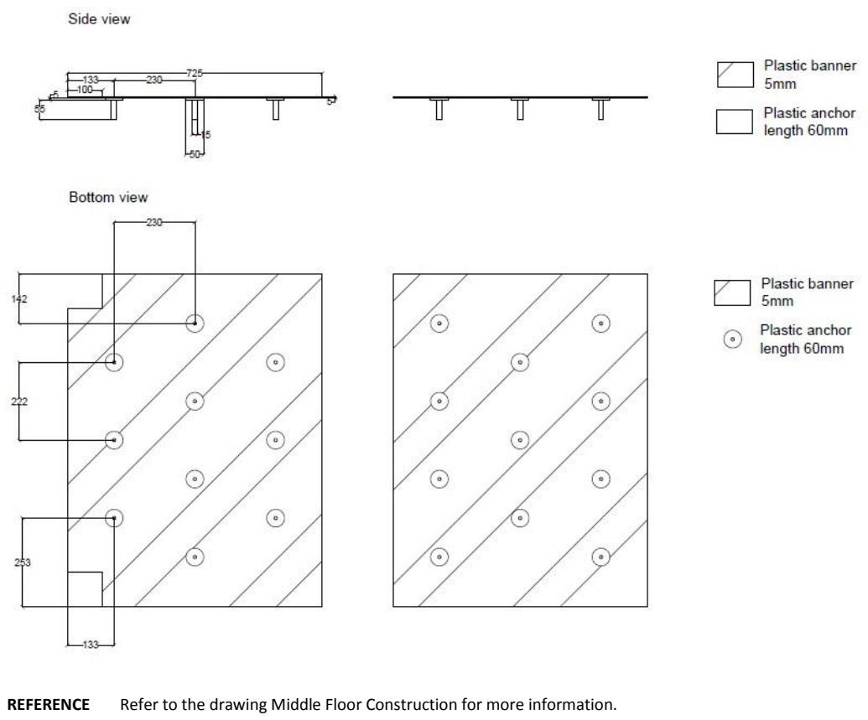
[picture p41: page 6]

REFERENCE Refer to the drawing Middle Floor Construction for more information.

## TOP BOARD

LIST OF MATERIALS:

- | Plastic board (used plastic banner) 75x100x0,5cm | 2PCS
- | Plastic board (used plastic banner) 72,5x95x0,5cm | 2PCS
- Glue for plastics
- | Plastic anchors for styrofoam heat insulation Length 12,5cm | 10PCS
- Plumbers putty

PROCEDURE:

Step 1 Glue smaller plastic boards to the bottom of larger ones. One edge should be aligned with the larger board while leaving even 2,5cm gap on other three sides.

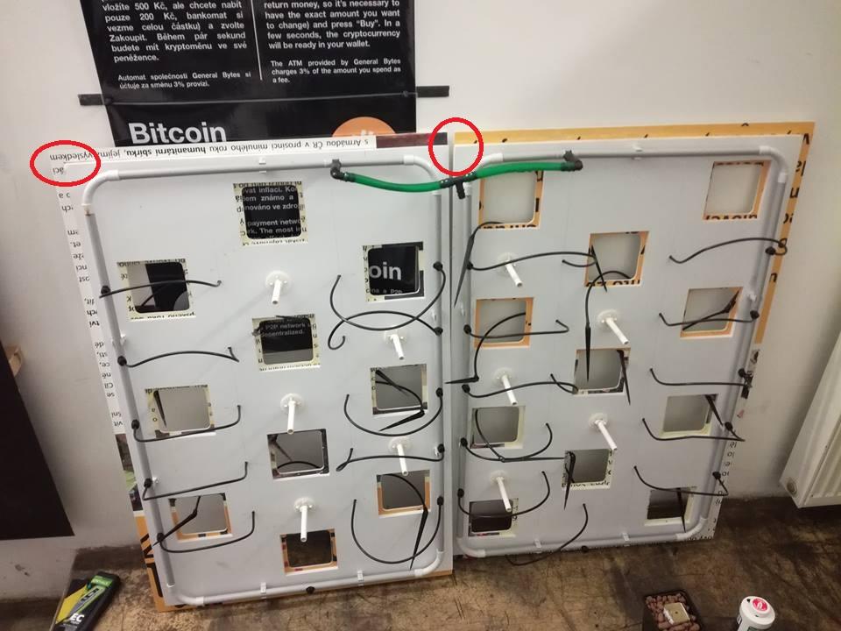
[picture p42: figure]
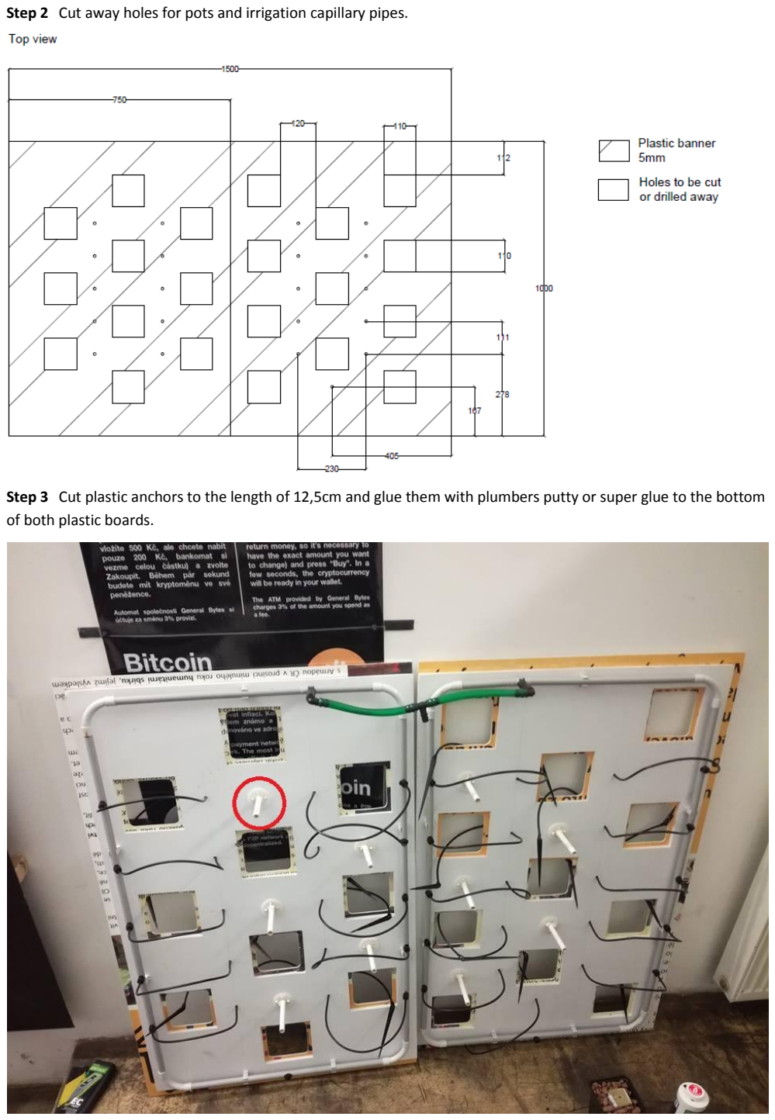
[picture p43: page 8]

Step 2 Cut away holes for pots and irrigation capillary pipes.
Step 3 Cut plastic anchors to the length of 12,5cm and glue them with plumbers putty or super glue to the bottom of both plastic boards.

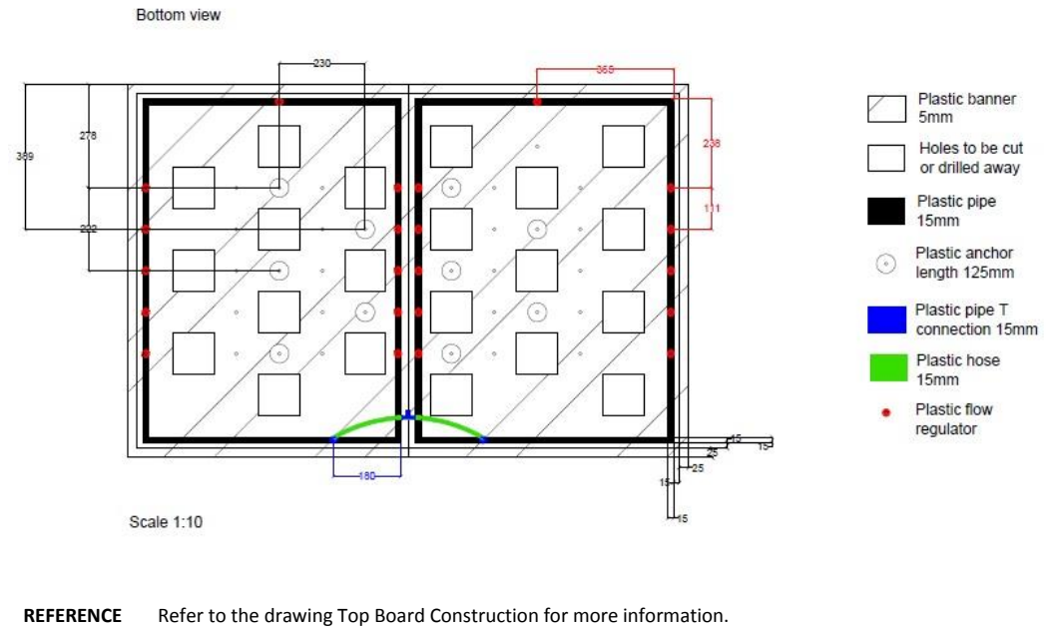
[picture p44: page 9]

REFERENCE Refer to the drawing Top Board Construction for more information.

## IRRIGATION

LIST OF MATERIALS:

- | Plastic pipe diameter 1,5cm holder | 14PCS
- | Plastic pipe diameter 1,5cm | 6m
- | Plastic pipe L connection diameter 1,5cm | 8PCS
- | Plastic pipe T connections diameter 1,5cm | 3PCS
- | Plastic hose diameter 1,5cm | 1m
- | Plastic hose L connections | 2PCS
- | Plastic flow regulator | 22PCS
- | Plastic capillary pipes 30cm | 21PCS
- | Dripping needles | 21PCS
- | Super glue | 1PC
- | Submersible water pump 750l/h | 1PC
- | Lever cable connectors | 2PCS

PROCEDURE:

Step 1 Glue plastic pipe holders to the bottom of the board (7pcs per board) with super glue.


Step 2 Cut plastic pipe in 4 pieces of 89cm and 4 pices of 66cm and connect them with L connections. Create two rectangular pipeline circuits.
Step 3 Cut two shorter plastic pipes and insert T connection..


Step 4 Drill small holes into the pipeline and insert flow regulators. Holes should be placed with similar distance to ensure even solution delivery. Note: One module should feed 11 plants, and the other one only 10. To distribute the solution evenly, install 11 flow regulators on both pipeline modules. The extra flow regulator installed in the growing board that feeds only 10 plants will be kept unused.


Step 5 Attach capillary pipes to flow regulators and put them through holes in the board. Then you may attach dripping needles to blank ends of capillary pipes. Note: One flow regulator on the board with 10 pot holes will remain blank.
Step 6 Finalize the construction with attaching the hose to inlets of pipeline modules. At the end use one T connection to join pipeline modules to one inlet. Hose should not be folded over to avoid water to move through the system easily.

Step 7 Cut the power cable of the pump near the socket plug, put the pump into the box and push the cable through the cable hole in the box. Join the cable again with cable connections.

2PICS

Step 8 Assemble the system. Put the middle floor inside the box and then install the top board.


Step 9 Connect the hose to the pump outlet.

REFERENCE: Refer to drawings Top Board Construction and Setup for more information.

## LIGHTING SYSTEM


LIST OF MATERIALS:

- | Wooden prism 150x3x2cm | 17PCS
- | Wooden prism 99x5x2cm | 3PCS
- | Nails length 3cm | 51PCS
- | Steel hooks with screws | 4PCS
- | Full spectrum LED lights SANlight M30 30W | 4PCS

PROCEDURE:

Step 1 Construct a grid out ouf wooden prisms with nails, and attach steel hooks to the top of the grid as per drawings.


Step 2 Hang wooden contruction to the ceiling.
Step 3 Attach lights to the construction and lead cables as needed.

REFERENCE Refer to the drawing Lighting System for more information.

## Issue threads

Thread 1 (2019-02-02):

Roadmap or to-do list

pryetranka, 2019-02-02:
Any plans for creating a roadmap or to-do list for the project? I would love to contribute, however, some specific directions and goals are needed for that first. Is there any vision for it or do you leave it completely open?

jhamat1, 2019-02-04:
We are finalizing the documentation...sorry for the inconvenience...it's our first open source project, and we are still learning. We will definitely keep uploading more materials, at first we will focus on the read me file to explain background and purpose of the project, and to outline visions for development. So far I'm sure we will be testing lights, organic fertilizers and organic substrates - in these areas we appreciate any feedback any time. Also we are planning to publish the IoT project of our colleagues who already implemented their initial version of the device at our box to publish complete HW and SW technologies. Thank you for your suggestion, we'll keep working on it ;)

Closed 2019-02-05.

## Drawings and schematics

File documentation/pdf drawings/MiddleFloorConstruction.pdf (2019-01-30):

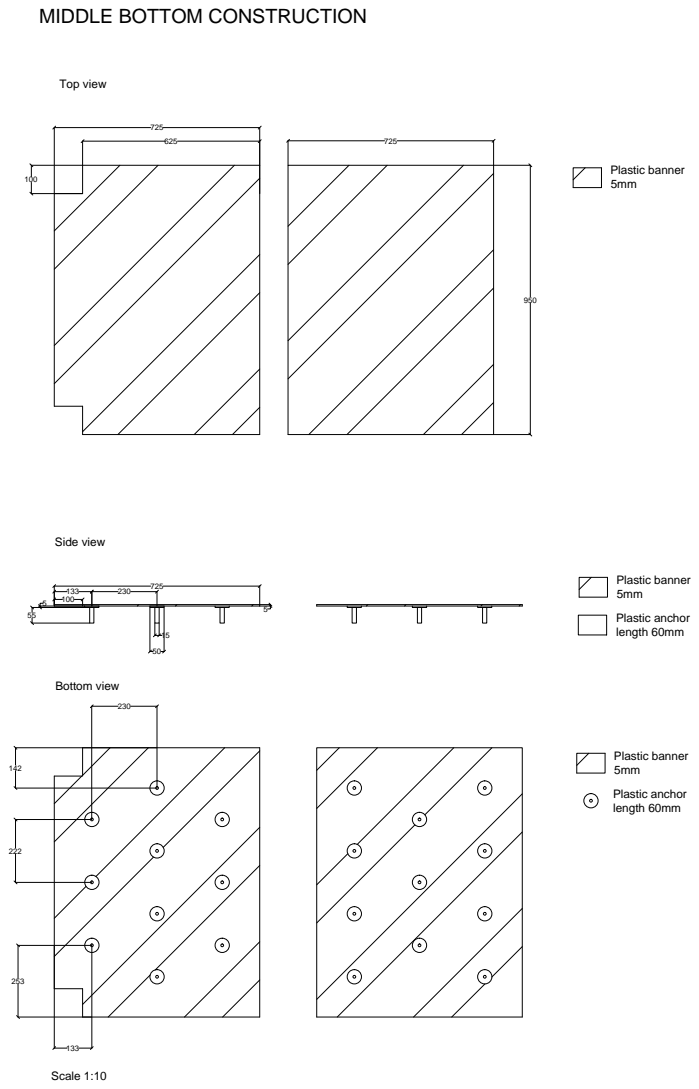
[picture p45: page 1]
Plastic banner; Plastic anchor length 60mm; Top view; Side view; Bottom view; Scale 1:10

MIDDLE BOTTOM CONSTRUCTION

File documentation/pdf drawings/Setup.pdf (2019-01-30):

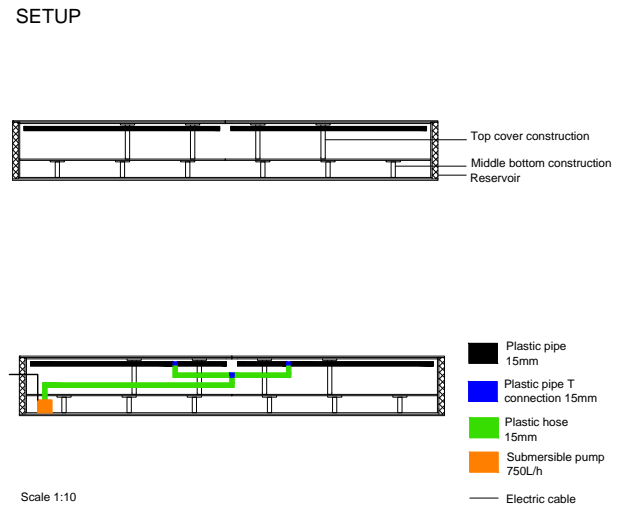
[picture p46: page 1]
Plastic pipe; Plastic hose; Plastic pipe T connection 15mm; Submersible pump; Scale 1:10; Electric cable

Top cover construction

Middle bottom construction
Reservoir

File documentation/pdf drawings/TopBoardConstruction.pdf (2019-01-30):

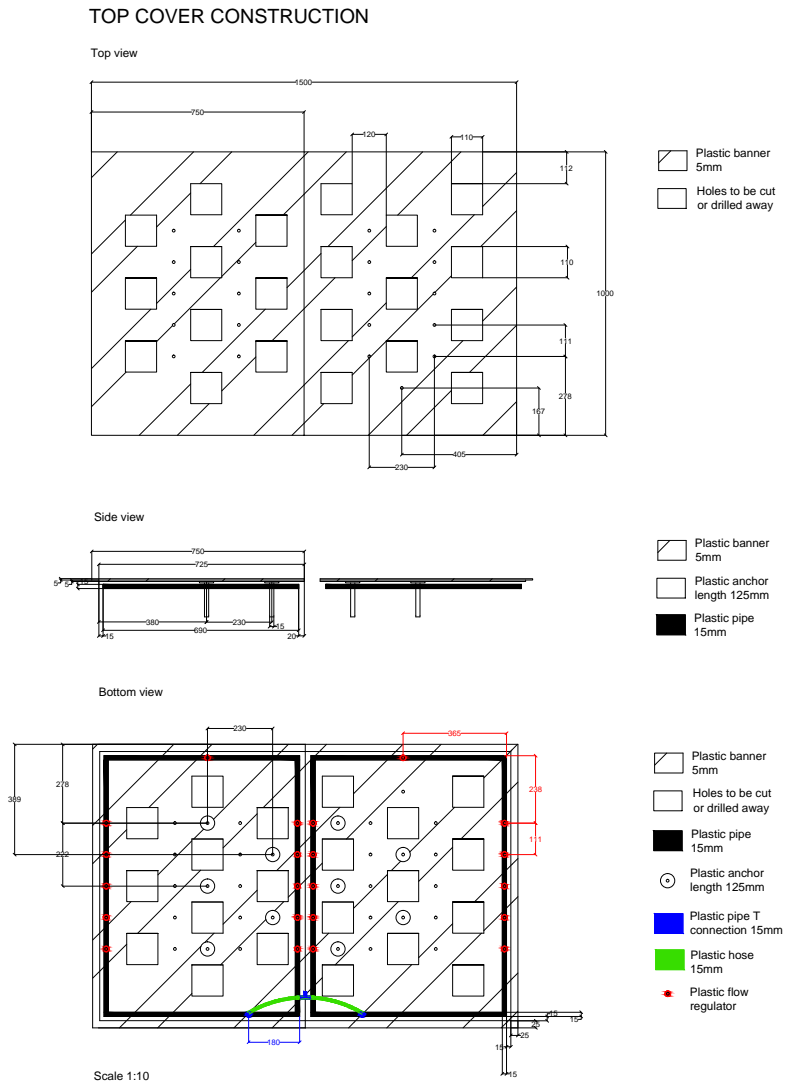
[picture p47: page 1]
Plastic banner; Plastic anchor length 125mm; Plastic pipe; Plastic hose; Plastic pipe T connection 15mm; Plastic flow; Scale 1:10; Top view; Side view; Bottom view

TOP COVER CONSTRUCTION

Holes to be cut
or drilled away

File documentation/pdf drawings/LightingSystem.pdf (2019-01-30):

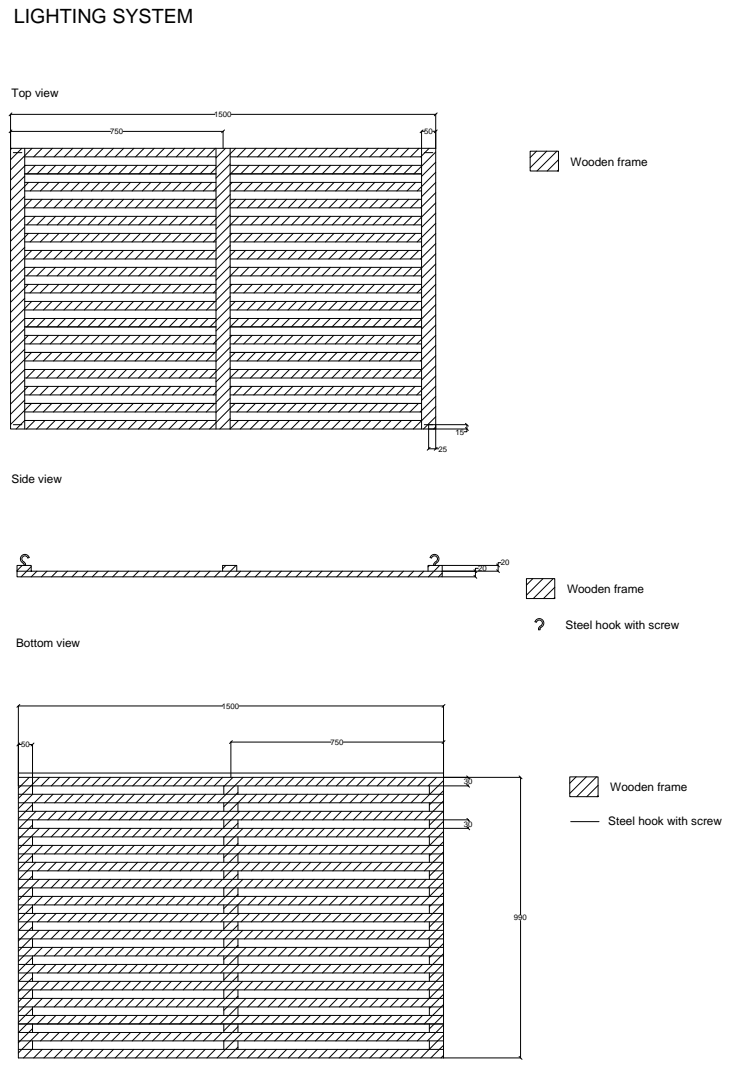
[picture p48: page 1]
LIGHTING SYSTEM; Wooden frame; Top view; Side view; Bottom view

Steel hook with screw

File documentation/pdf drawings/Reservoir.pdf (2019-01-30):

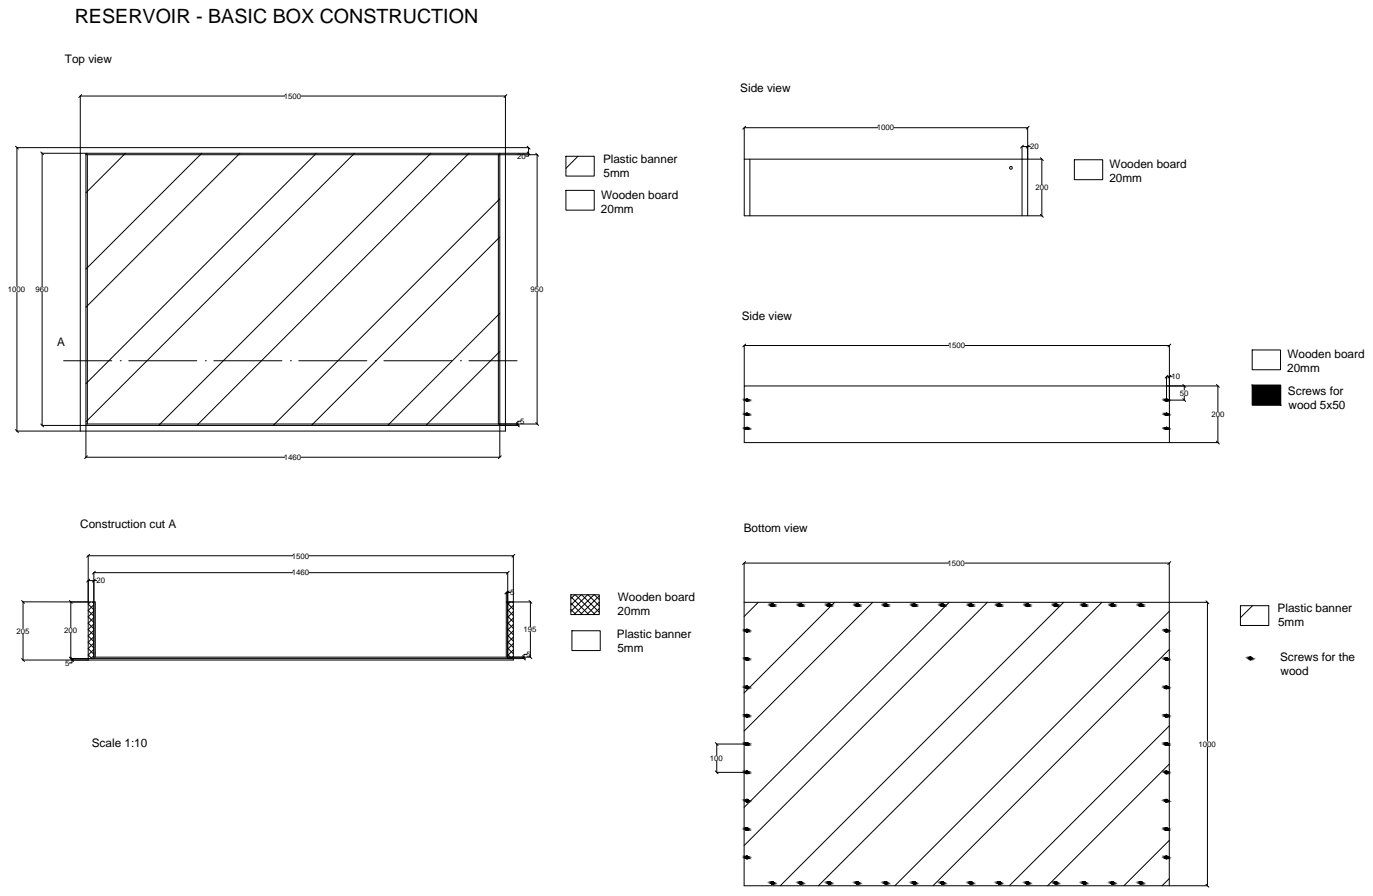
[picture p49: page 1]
Plastic banner; Wooden board; Screws for wood 5x50; Top view; Side view; Construction cut A; Scale 1:10; Bottom view

RESERVOIR - BASIC BOX CONSTRUCTION

Screws for the
wood
